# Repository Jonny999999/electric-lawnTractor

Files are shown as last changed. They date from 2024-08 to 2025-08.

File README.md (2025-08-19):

# Throttle Tune – Throttle Adapter for BLDC Motor Controllers

A microcontroller-based board with a PWM-based analog output (RC filter + buffer) to emulate a DAC.
The goal is to improve throttle response and add configurable driving modes to cheap BLDC motor controllers (e.g. 3000 W BLDC "go-kart kit" controllers).  

Currently it is used in the [electric Kettcar conversion](https://pfusch.zone/electric-kettcar.html) with a 3000 W BLDC drive, this board fixes the controller’s unusable throttle mapping and makes the vehicle smooth and controllable adding a lot of flexibility.

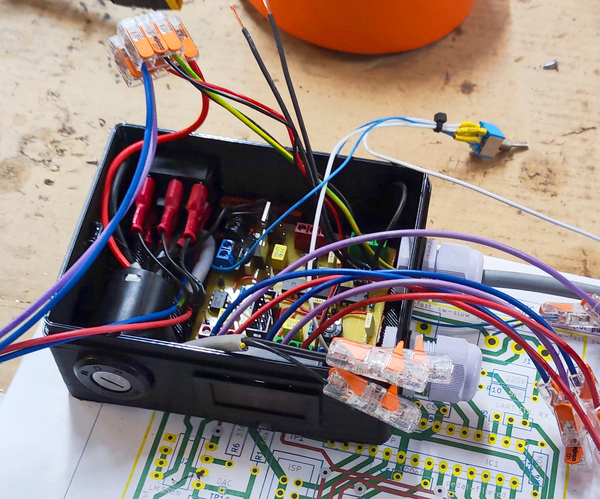
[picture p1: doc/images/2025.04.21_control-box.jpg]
  

*Control box with the custom pcb connected between throttle and motor controller*  
*Contains: PCB, key switch, battery indicator, several UI switches*

---

## Problem

Cheap BLDC controllers (such as KT-style 3000 W kits) have several issues:
- No configuration options at all
- Speed levels provided by the controller are usually defined poorly
- Only ~2 cm (~60 %) of gas pedal travel is actually used
- Jerky, hard-to-control acceleration (tiny pedal movements cause extreme changes in power - positive feedback when accelerating thus pressing the pedal more makes this even worse)

Using only the original setup makes smooth low-speed driving or child-friendly operation nearly impossible

---

## Solution

The **Throttle Tune** board sits between the analog throttle pedal (or handle) and the motor controller.  
It rescales, filters, and manipulates the signal (fading, modes...) while adding safety and convenience features.

---

## Features

### Firmware
- **Throttle remap**: use full pedal range (configure in/out ranges)
- **Ramp-up / fade**: prevents stuttering, smoother control (configurable max rate of change)
- **Speed modes**: 3 levels + hidden "Sport" mode (highly configurable - several parameters on per-mode-basis)
- **Reverse scaling**: reduced throttle in reverse
- **Buzzer alerts**: startup-, reverse-, mode switch beeps

### Hardware
- ATmega8 microcontroller
- Custom DAC output (0–5 V) to motor controller (implementation: PWM output -> lowpass -> buffer)
- CNC-milled single-sided PCB
- Through-hole components (easy to build/repair)
- 3D-printed enclosure
- Inputs: Hall pedal, reverse switch, speed selector
- Outputs: DAC to controller, buzzer

---

## Hardware

### Schematic
[pcb_throttle-tune/export/schematic.pdf](pcb_throttle-tune/export/schematic.pdf)  


### Layout


### PCB Photo
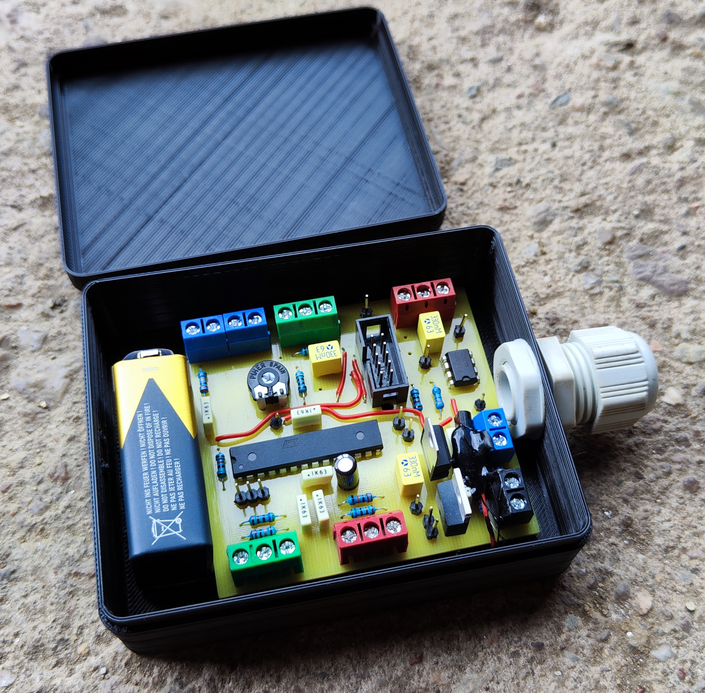
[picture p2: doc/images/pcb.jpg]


---

## Example Applications

### Electric Kettcar
Documentation: [pfusch.zone/electric-kettcar](https://pfusch.zone/electric-kettcar)

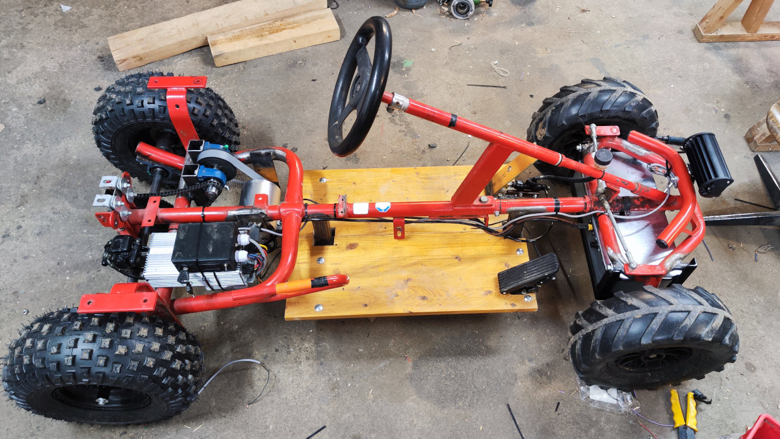
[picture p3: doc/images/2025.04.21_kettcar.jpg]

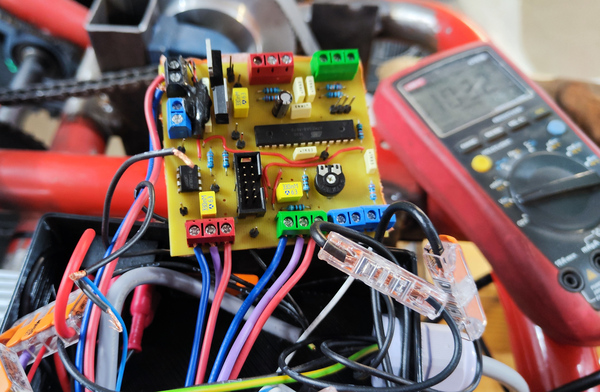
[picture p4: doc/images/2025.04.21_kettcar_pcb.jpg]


*Wiring of PCB between pedal and controller (right) and the finished vehicle (left).*

---

### Electric Lawn Tractor (temporary use-case)
Documentation: [pfusch.zone/electric-lawn-tractor](https://pfusch.zone/electric-lawn-tractor)

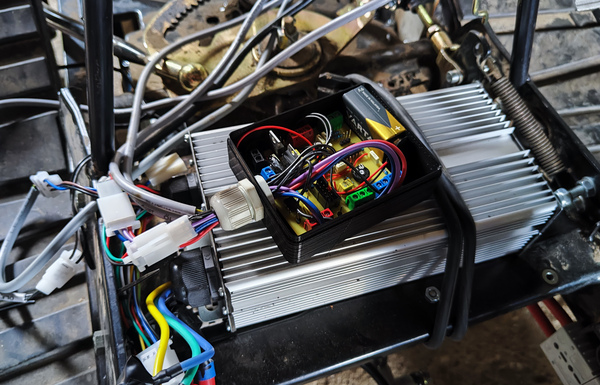
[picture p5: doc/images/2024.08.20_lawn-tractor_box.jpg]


*Throttle Tune board inside in box on top of the motor controller, battery powered (earlier project - initial but temporary use).*

---

## Repository Content
- `pcb_throttle-tune/` – KiCad project, schematic, layout exports
- `fw_throttle-tune/` – AVR firmware (ATmega8)
- `doc/images` – photos of the build and control box

---

## Usage

### Wiring
See [pcb_throttle-tune/export/layout.pdf](pcb_throttle-tune/export/layout.pdf) for what needs to be connected to which terminals.

### Adjust thresholds
Several config options (macro variables) are defined at the top of `main.c` (see detailed comments).
These include controller start/max voltage, pedal min/max voltage, idle voltage, etc.  
To calibrate:  
- Wire everything up  
- Enable `DEBUG_UART_DEBUG_OUTPUT_ENABLED`  
- Build and flash the firmware
- Connect a USB-UART adapter (header pins next to mcu, TX + GND are enough)  
- Play with the throttle and observe the UART logs to determine the values  
- Adjust the macros in `main.c` accordingly, compile, flash, try again

### Configure / Adjust modes
Driving modes are selected via 2 GPIO pins, each with its own config in the `modeConfigs[]` array.  
Parameters can be tuned per mode using this struct:
```c
//=============================
//==== Mode configuration =====
//=============================
typedef struct {
    const char *name;
    uint8_t maxPercent;     // percent of max possible speed applied at full throttle
    uint8_t maxPercentReverse;
    uint8_t beepCount;      // count beeped when entering this mode
    uint16_t rampUpStep;    // max duty increment per interval (max 1023)
    uint16_t rampUpIntervalMs; // note: must be larger than cycle time (consider when UART used alot)
    uint8_t pedalAverageWindowSize; // window size of the moving average to smooth pedal input (0 = disabled)
    // Future: pedal averaging, throttle curve, etc.
} kettcarConfig_t;
```
See comments in main.c and adjust as needed.

### Build & Flash
#### Install Requirements
```bash
yay -S avr-gcc avr-libc make
```

#### Build
```bash
cd fw_throttle-tune/
make
```

#### Flash
Connect avr controller using USBASP V2.0 ISP programmer using the 10pin connector on the pcb
```bash
cd fw_throttle-tune/
make                # compile firmware first
sudo make upload    # flash to MCU via USBasp
```
Note: Be sure to recompile before flashing, or you may upload an old build...

---

## TODO (future hardware rev)
- Add TVS diode  
- Add buzzer footprint (currently wired to spare pin and implemented in firmware, but not documented in pcb design)  
- Drop unused terminals (see notes design)
- Add reverse polarity protection
- Add onboard buck converter to be used with e.g. 72V directly not requiring external converter

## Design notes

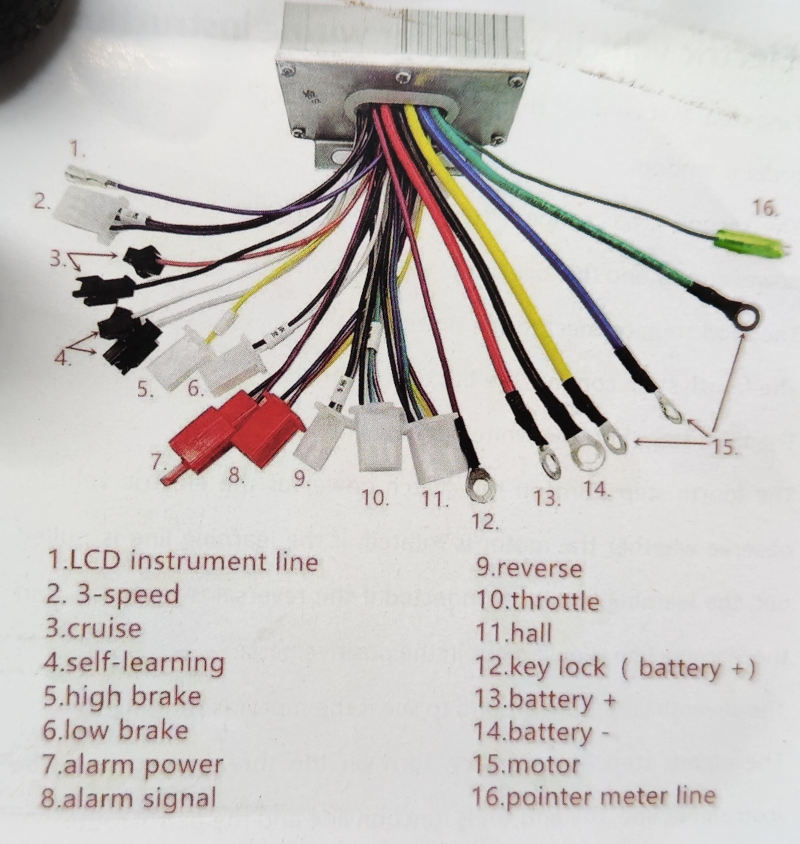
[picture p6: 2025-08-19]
doc/images/3000W-controller_wire-assignment.jpg

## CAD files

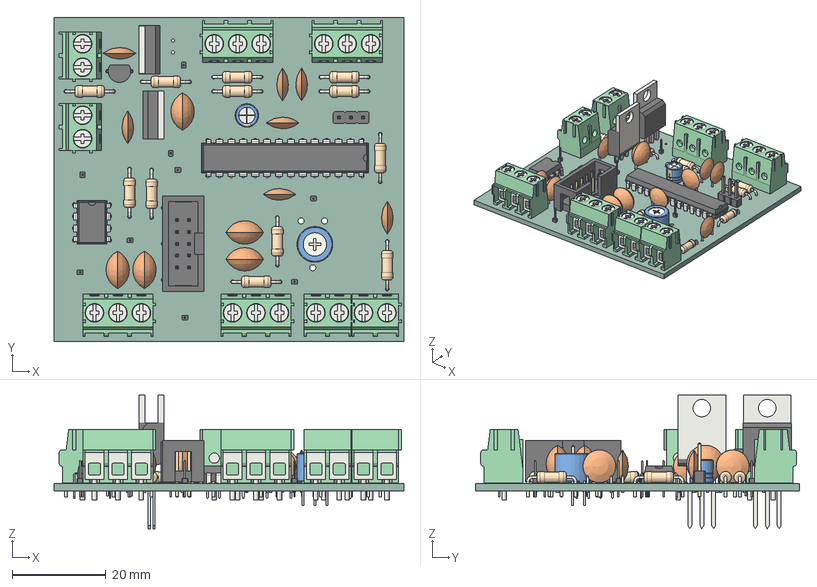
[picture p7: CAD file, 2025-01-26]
pcb_throttle-tune/export/throttle-tune.step
74.7 x 69.1 x 28.5 mm
TerminalBlock_Phoenix_PT_15_2_50_H_1x02_P500mm_Horizontal x 4
C_Disc_D70mm_W25mm_P500mm x 7
R_Axial_DIN0207_L63mm_D25mm_P1016mm_Horizontal x 12
TerminalBlock_Phoenix_PT_15_3_50_H_1x03_P500mm_Horizontal x 4
PinHeader_1x01_P100mm_Vertical x 9
Potentiometer_Bourns_3339P_Vertical
TO-92_Inline_Wide
C_Disc_D80mm_W50mm_P500mm x 5
DIP-8_W7.62mm
TO-220-3_Vertical x 2
PinHeader_1x03_P254mm_Vertical
DIP-28_W7.62mm
IDC_Header_2x05_P254mm_Vertical
CP_Radial_D50mm_P250mm
throttle-tune_PCB

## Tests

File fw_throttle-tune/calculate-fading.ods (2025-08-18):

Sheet: interval-variable_step-fixed
kettcar throttle-tune pcb: determine fading related config options for the different modes
 | rampUpIntervalMs | Resulting 0 to 100 time ms note: depending on level only e.g. 0 to 40% is actually used | Resulting time from 0 to maxDuty
 | 1 | 248 | 37 |  | CONFIG
 | 2 | 495 | 74 |  | CONTROLLER_MAX | 670
 | 3 | 743 | 111 |  | CONTROLLER_MIN | 175
 | 4 | 990 | 149
 | 5 | 1238 | 186
 | 6 | 1485 | 223 |  | rampUpStep | 2
 | 7 | 1733 | 260
 | 8 | 1980 | 297 |  | maxDuty (mode) | 15
 | 9 | 2228 | 334
 | 10 | 2475 | 371
 | 11 | 2723 | 408
 | 12 | 2970 | 446 | Goal: select config options rampUpStep and rampUpIntervalMs Howto: try different rampUpdateIntervalMs and search&select rampUpStep line to achive desired time to maxDuty / 100% Its probably a good idea to have small step for max smoothness/resolution
 | 13 | 3218 | 483
 | 14 | 3465 | 520
 | 15 | 3713 | 557
 | 16 | 3960 | 594
 | 17 | 4208 | 631
 | 18 | 4455 | 668
 | 19 | 4703 | 705
 | 20 | 4950 | 743
 | 21 | 5198 | 780
 | 22 | 5445 | 817
 | 23 | 5693 | 854
 | 24 | 5940 | 891
 | 25 | 6188 | 928
 | 26 | 6435 | 965
 | 27 | 6683 | 1002
 | 28 | 6930 | 1040
 | 29 | 7178 | 1077
 | 30 | 7425 | 1114
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

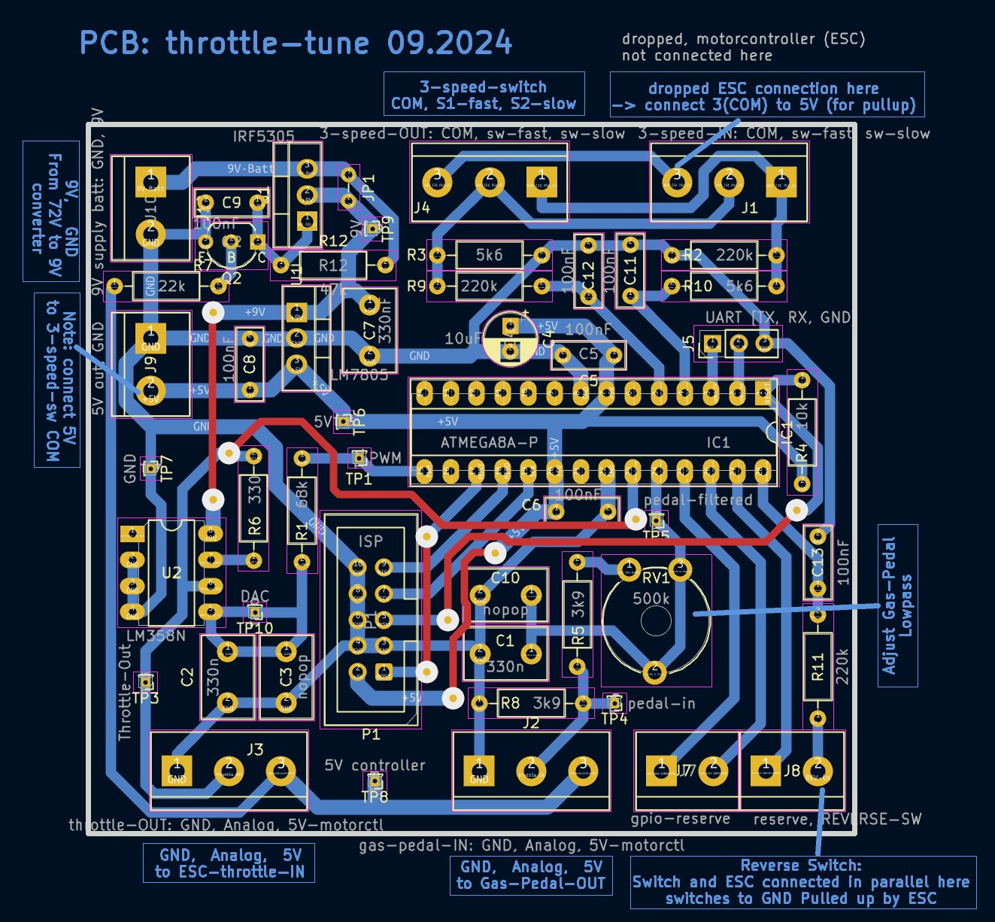
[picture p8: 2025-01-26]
pcb_throttle-tune/export/layout.jpg

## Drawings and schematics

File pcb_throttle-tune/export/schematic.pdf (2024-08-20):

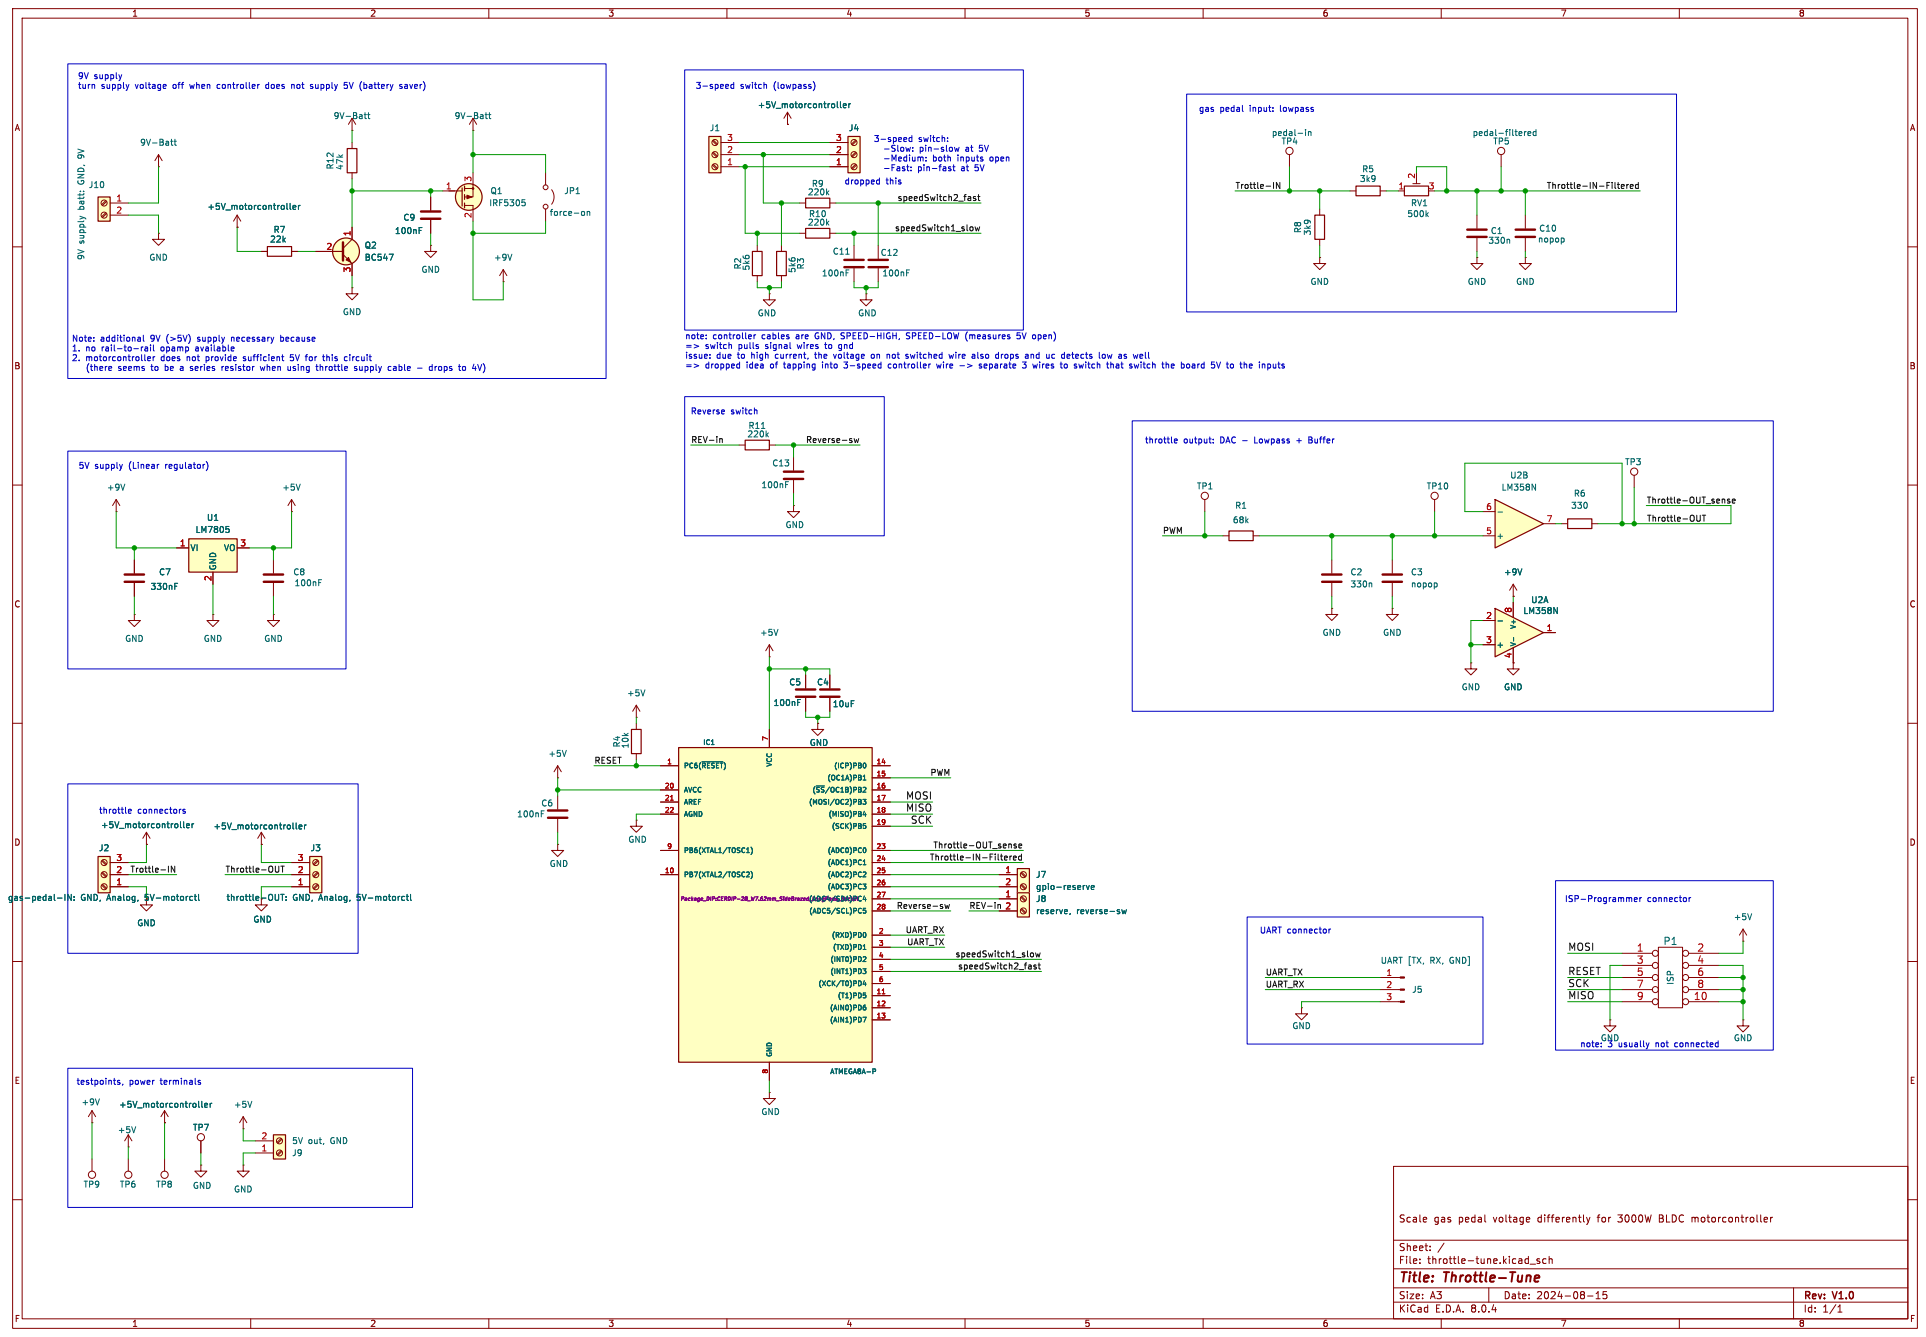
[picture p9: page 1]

IRF5305
REV-in Throttle-IN-Filtered Reverse-sw

note: 3 usually not connected

Id: 1/1 Title: Throttle-Tune

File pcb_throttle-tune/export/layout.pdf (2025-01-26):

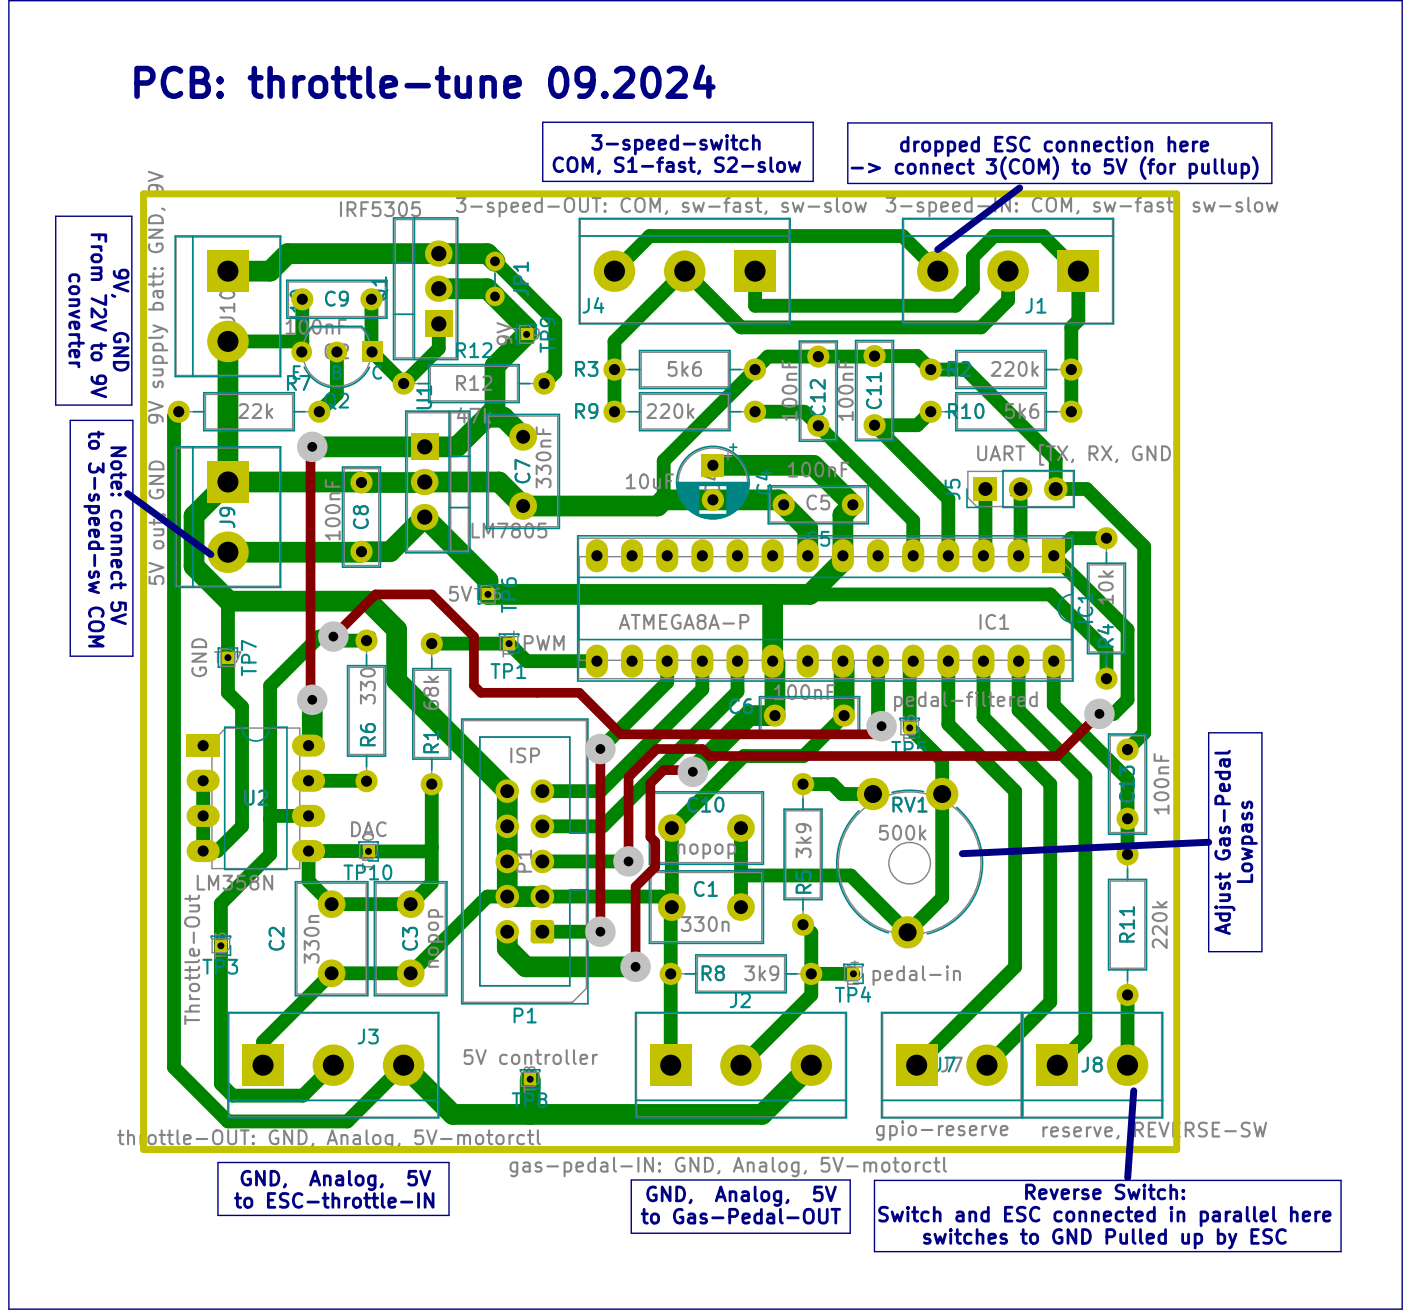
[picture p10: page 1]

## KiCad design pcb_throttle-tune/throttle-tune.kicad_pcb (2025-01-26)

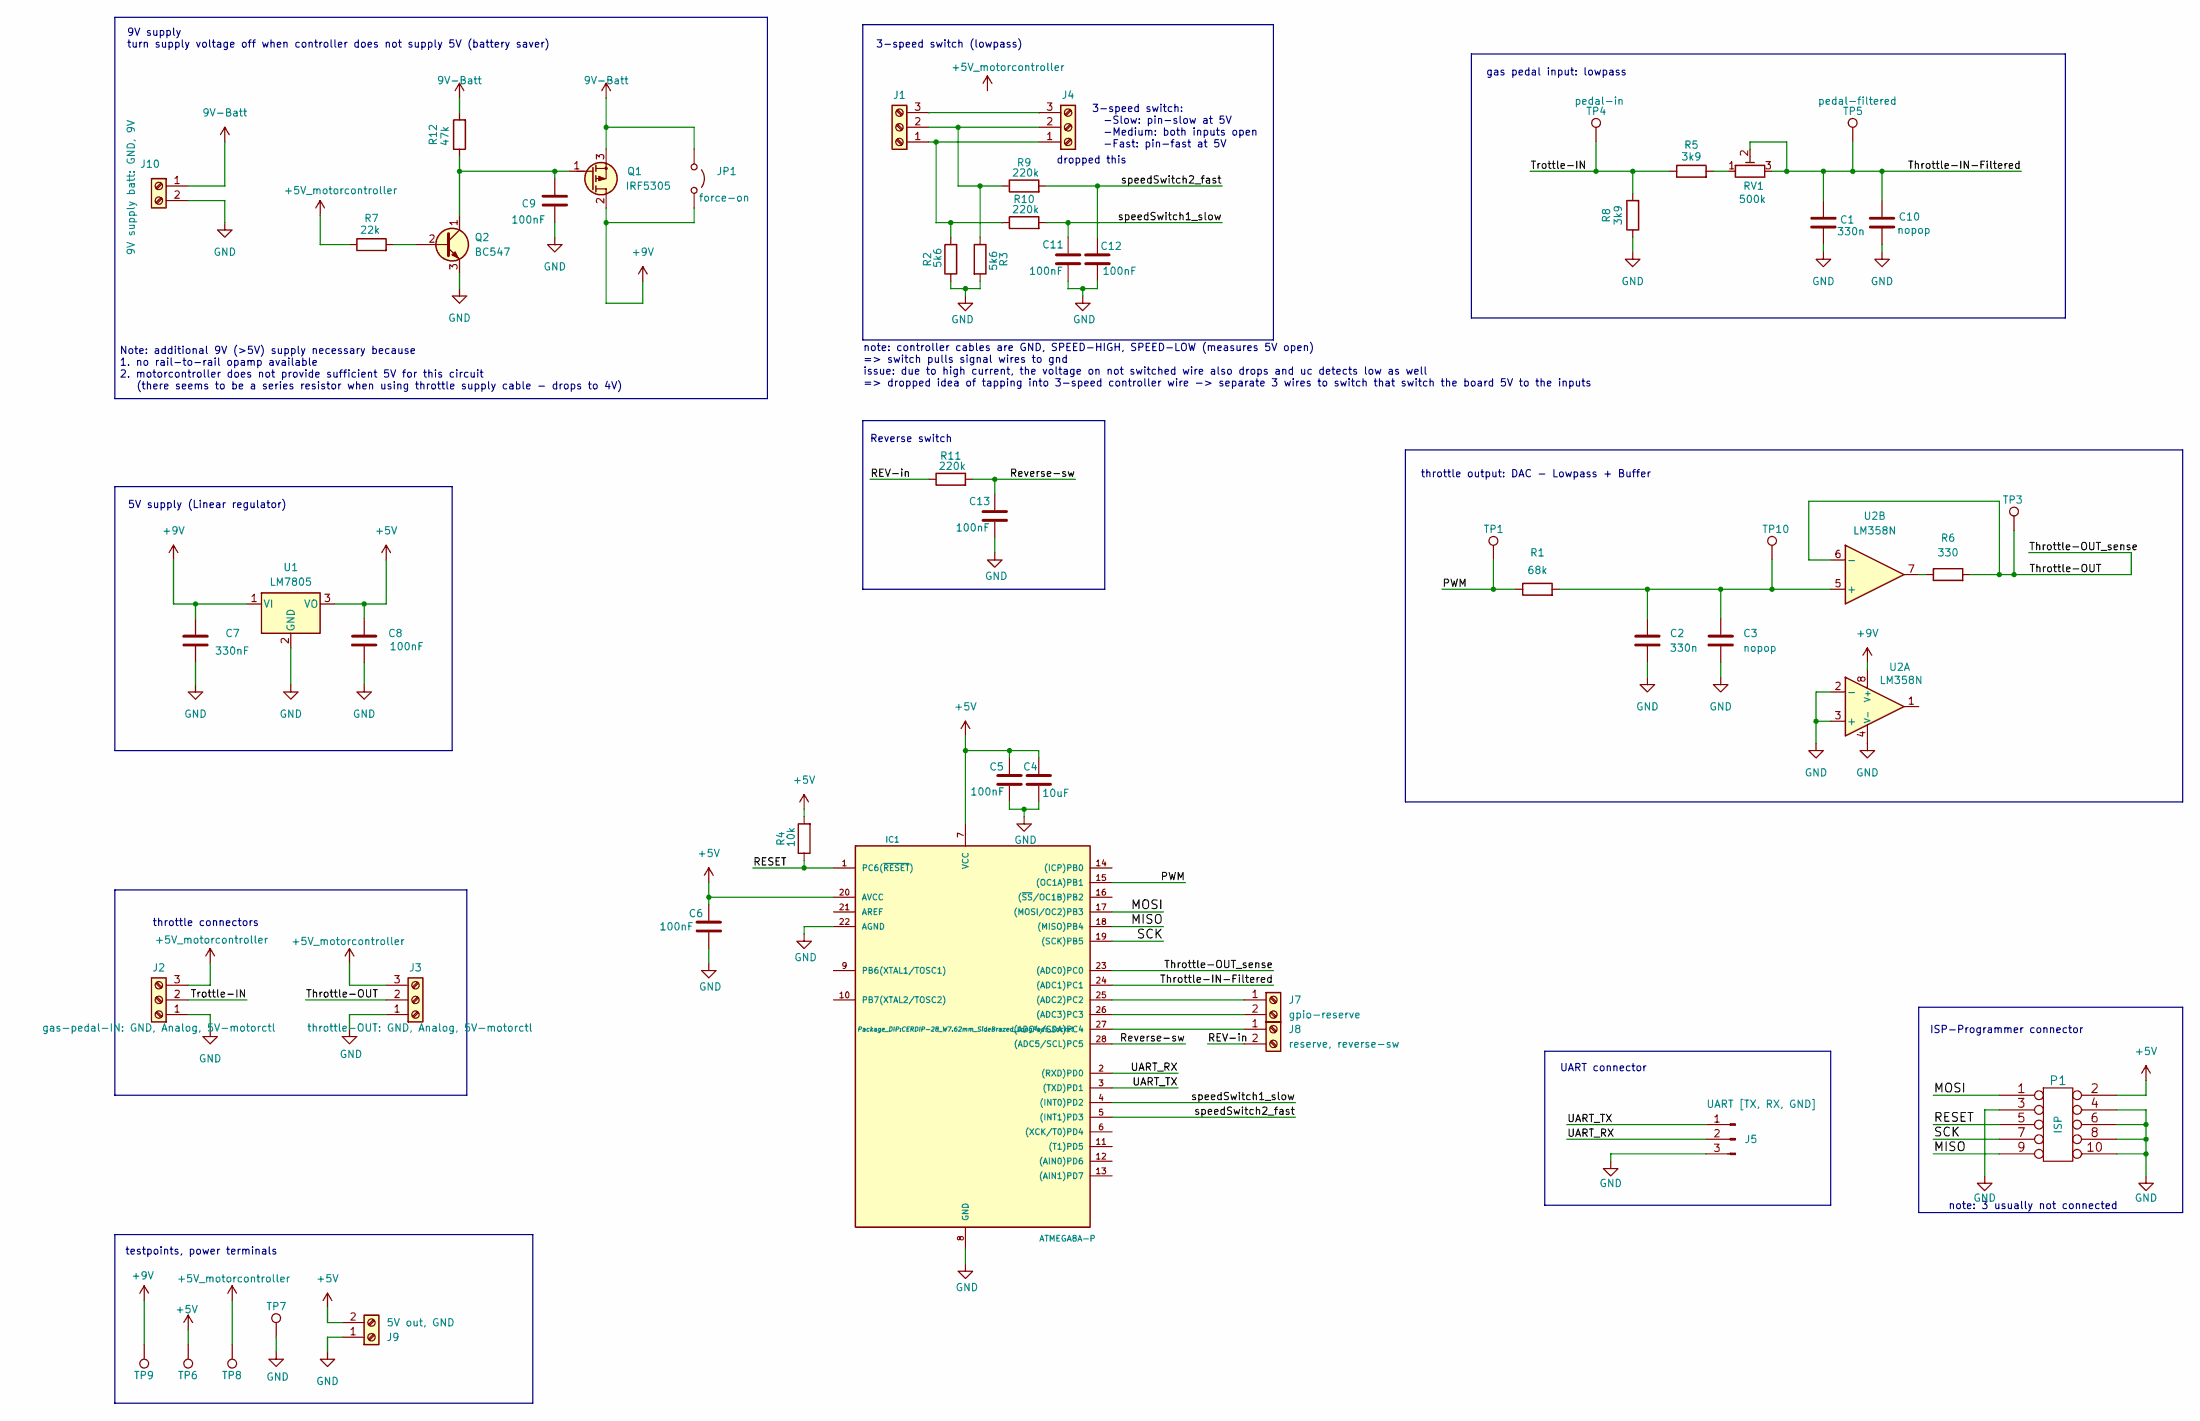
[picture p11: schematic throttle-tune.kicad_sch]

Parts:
C1, C2: 330n; C_Disc_D8.0mm_W5.0mm_P5.00mm
C3, C10: nopop; C_Disc_D8.0mm_W5.0mm_P5.00mm
C4: 10uF; CP_Radial_D5.0mm_P2.50mm
C5, C6, C8, C9, C11, C12, C13: 100nF; C_Disc_D7.0mm_W2.5mm_P5.00mm
C7: 330nF; C_Disc_D8.0mm_W5.0mm_P5.00mm
IC1: ATMEGA8A-P; CERDIP-28_W7.62mm_SideBrazed_LongPads_Socket
J1: 3-speed-IN: COM, sw-fast, sw-slow; TerminalBlock_bornier-3_P5.08mm
J2: gas-pedal-IN: GND, Analog, 5V-motorctl; TerminalBlock_bornier-3_P5.08mm
J3: throttle-OUT: GND, Analog, 5V-motorctl; TerminalBlock_bornier-3_P5.08mm
J4: 3-speed-OUT: COM, sw-fast, sw-slow; TerminalBlock_bornier-3_P5.08mm
J5: UART [TX, RX, GND]; PinHeader_1x03_P2.54mm_Vertical
J7: gpio-reserve; TerminalBlock_bornier-2_P5.08mm
J8: reserve, reverse-sw; TerminalBlock_bornier-2_P5.08mm
J9: 5V out, GND; TerminalBlock_bornier-2_P5.08mm
J10: 9V supply batt: GND, 9V; TerminalBlock_bornier-2_P5.08mm
JP1: force-on; Jumper_P2.54mm_D0.7mm
P1: ISP; IDC-Header_2x05_P2.54mm_Vertical
Q1: IRF5305; TO-220-3_Vertical
Q2: BC547; TO-92_Inline_Wide_CBE
R1: 68k; R_Axial_DIN0207_L6.3mm_D2.5mm_P10.16mm_Horizontal
R2, R3: 5k6; R_Axial_DIN0207_L6.3mm_D2.5mm_P10.16mm_Horizontal
R4: 10k; R_Axial_DIN0207_L6.3mm_D2.5mm_P10.16mm_Horizontal
R5, R8: 3k9; R_Axial_DIN0207_L6.3mm_D2.5mm_P10.16mm_Horizontal
R6: 330; R_Axial_DIN0207_L6.3mm_D2.5mm_P10.16mm_Horizontal
R7: 22k; R_Axial_DIN0207_L6.3mm_D2.5mm_P10.16mm_Horizontal
R9, R10, R11: 220k; R_Axial_DIN0207_L6.3mm_D2.5mm_P10.16mm_Horizontal
R12: 47k; R_Axial_DIN0207_L6.3mm_D2.5mm_P10.16mm_Horizontal
RV1: 500k; Potentiometer_Piher_PT-10-V10_Vertical
TP1: PWM; PinHeader_1x01_P1.00mm_Vertical
TP3: Throttle-Out; PinHeader_1x01_P1.00mm_Vertical
TP4: pedal-in; PinHeader_1x01_P1.00mm_Vertical
TP5: pedal-filtered; PinHeader_1x01_P1.00mm_Vertical
TP6: 5V; PinHeader_1x01_P1.00mm_Vertical
TP7: GND; PinHeader_1x01_P1.00mm_Vertical
TP8: 5V controller; PinHeader_1x01_P1.00mm_Vertical
TP9: 9V; PinHeader_1x01_P1.00mm_Vertical
TP10: DAC; PinHeader_1x01_P1.00mm_Vertical
U1: LM7805; TO-220-3_Vertical
U2: LM358N; DIP-8_W7.62mm_LongPads

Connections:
9V-Batt: J10.1, JP1.1 (A), Q1.3 (S), R12.2
+5V: C4.1, C5.1, C6.1, C8.1, IC1.7 (VCC), IC1.20 (AVCC), J9.2, P1.2, R4.2, TP6.1, U1.3 (VO)
+5V_motorcontroller: J2.3, J3.3, R7.1, TP8.1
+9V: C7.1, JP1.2 (B), Q1.2 (D), TP9.1, U1.1 (VI), U2.8 (V+)
/MISO: IC1.18 ((MISO)PB4), P1.9
/MOSI: IC1.17 ((MOSI/OC2)PB3), P1.1
/PWM: IC1.15 ((OC1A)PB1), R1.1, TP1.1
/RESET: IC1.1 (PC6(~RESET)), P1.5, R4.1
/REV-in: J8.2, R11.1
/Reverse-sw: C13.1, IC1.28 ((ADC5/SCL)PC5), R11.2
/SCK: IC1.19 ((SCK)PB5), P1.7
/Throttle-IN-Filtered: C1.1, C10.1, IC1.24 ((ADC1)PC1), RV1.2, RV1.3, TP5.1
/Throttle-OUT: IC1.23 ((ADC0)PC0), J3.2, R6.2, TP3.1, U2.6 (-)
/Trottle-IN: J2.2, R5.1, R8.2, TP4.1
/UART_RX: IC1.2 ((RXD)PD0), J5.2
/UART_TX: IC1.3 ((TXD)PD1), J5.1
/speedSwitch1_slow: C11.1, IC1.4 ((INT0)PD2), R10.2
/speedSwitch2_fast: C12.1, IC1.5 ((INT1)PD3), R9.2
GND: C1.2, C2.2, C3.2, C4.2, C5.2, C6.2, C7.2, C8.2, C9.2, C10.2, C11.2, C12.2, C13.2, IC1.8 (GND), IC1.22 (AGND), J2.1, J3.1, J5.3, J9.1, J10.2, P1.3, P1.4, P1.6, P1.8, P1.10, Q2.3 (E), R2.1, R3.2, R8.1, TP7.1, U1.2 (GND), U2.2 (-), U2.3 (+), U2.4 (V-)
unnamed: IC1.25 ((ADC2)PC2), J7.1
unnamed: IC1.26 ((ADC3)PC3), J7.2
unnamed: IC1.27 ((ADC4/SDA)PC4), J8.1
unnamed: J1.1, J4.1, R2.2, R10.1
unnamed: J1.2, J4.2, R3.1, R9.1
unnamed: J1.3, J4.3
unnamed: C9.1, Q1.1 (G), Q2.1 (C), R12.1
unnamed: Q2.2 (B), R7.2
unnamed: R5.2, RV1.1
unnamed: R6.1, U2.7
unnamed: C2.1, C3.1, R1.2, TP10.1, U2.5 (+)

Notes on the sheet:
throttle output: DAC - Lowpass + Buffer
note: controller cables are GND, SPEED-HIGH, SPEED-LOW (measures 5V open) => switch pulls signal wires to gnd issue: due to high current, the voltage on not switched wire also drops and uc detects low as well => dropped idea of tapping into 3-speed controller wire -> separate 3 wires to switch that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
throttle connectors
UART connector
3-speed switch (lowpass)
9V supply turn supply voltage off when controller does not supply 5V (battery saver)
note: 3 usually not connected
Note: additional 9V (>5V) supply necessary because 1. no rail-to-rail opamp available 2. motorcontroller does not provide sufficient 5V for this circuit (there seems to be a series resistor when using throttle supply cable - drops to 4V)
dropped this
gas pedal input: lowpass
5V supply (Linear regulator)
testpoints, power terminals
ISP-Programmer connector
3-speed switch: -Slow: pin-slow at 5V -Medium: both inputs open -Fast: pin-fast at 5V
Reverse switch

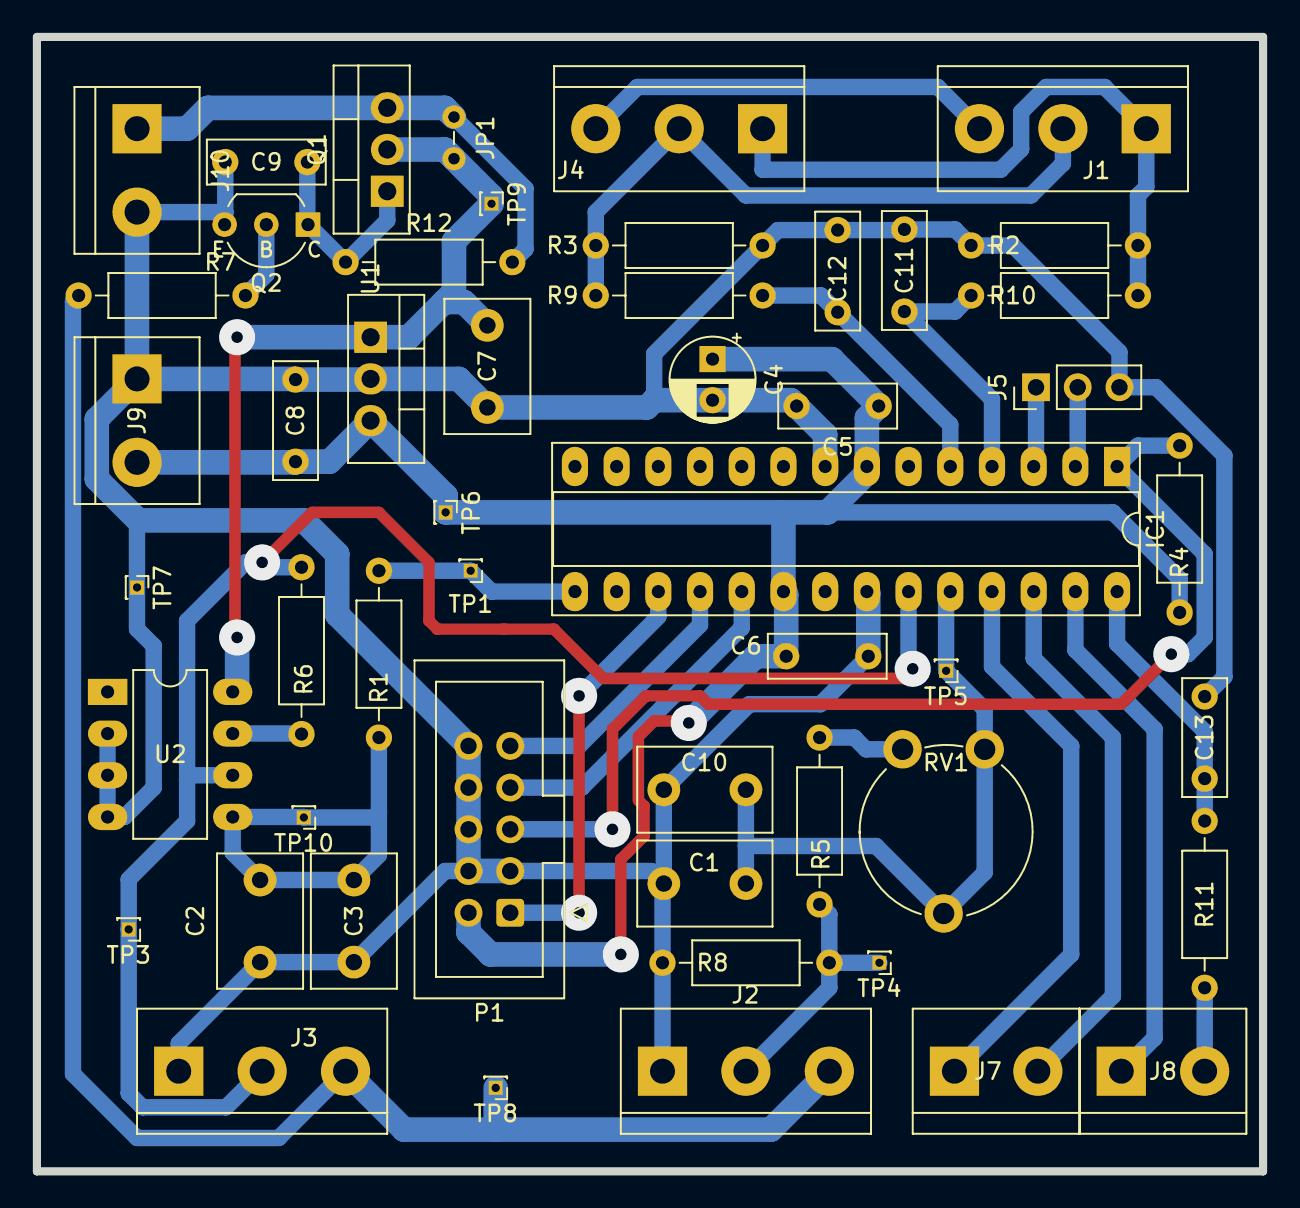
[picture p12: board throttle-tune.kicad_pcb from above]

Board: 2 copper layers, 74.7 x 69.1 mm, 51 parts (0 on the bottom side), 30 nets.

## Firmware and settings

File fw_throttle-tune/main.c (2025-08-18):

#include <avr/io.h>
#include <util/delay.h>
#include "usart.h"
#include "a2d.h"

#include "gpio.h"
#include "time.h"
#include "pwm.h"
#include "stdbool.h"

//====================
//====== config ======
//====================
// debugging
#define DEBUG_UART_DEBUG_OUTPUT_ENABLED 0 // log several variables for debugging the firmware
#define DEBUG_UART_DEBUG_OUTPUT_INTERVAL_MS 500 // interval the variables are logged (limit rate to have cycles for rest of firmware)
#define DEBUG_LOG_CYCLE_SPEED 0 // log main loop cycle count per 1000ms (to determine if set intervals are even realistic -> should always be higher than 1000 so we have 1ms resolution)
#define DEBUG_PASS_THROUGH 0 //if defined duty/output voltage is set to the same as input voltage (test hardware)

// thresholds (adc values, determined/tested with debug output)
#define GAS_PEDAL_MAX 630 // actual 660 no force / 697 with force
#define GAS_PEDAL_MIN 200 // actual 171 - note weird behaviour: when pressing decreases to 160 first then increases to MAX 

// thresholds the out voltage is scaled in between (0-100% speed)
#define CONTROLLER_START 250  // 250 starts, 246 stops (TODO: start higher?)
#define CONTROLLER_MAX 600 // hard to determine precisely

#define CONTROLLER_IDLE_DUTY 190 // keep some voltage when off, to prevent controller from going into fault mode
#define CONTROLLER_FULL_SPEED_DUTY 800
// duty set at 100% target speed (slightly higher than CONTROLLER_MAX ) to be sure to reach actual maximum speed even when CONTROLLER_MAX is slightly too low / we got noise

//--- fading ---
// track/estimate motor rpm/rolling out for quicker resume (start fading up from memory instead of 0)
// 6, 50ms -> 4s to decay from 100% to 0% 
#define DUTY_MEMORY_DECAY_INTERVAL_MS 50
#define DUTY_MEMORY_DECAY_STEP 4 // max 1023

// misc
#define BEEP_AT_REV_SW_CHANGE 1
#define PEDAL_SAMPLE_INTERVAL_MS 5 // minimum ms passed between sampling the pedal adc -> significantly affects moving average, but compensated by macro during config
#define PEDAL_SMOOTHING_MAX_WINDOW_SIZE 255 // max history of pedal adc values that can be kept for moving average



//--- configure GPIO Pins ---
// buzzer
const GPIO_Pin buzzerPin = {PC3, &PORTC, &DDRC, &PINC};

// speed switch
const GPIO_Pin speedSwitch_slow = {PD2, &PORTD, &DDRD, &PIND};
const GPIO_Pin speedSwitch_fast = {PD3, &PORTD, &DDRD, &PIND};
const GPIO_Pin reverseSwitch = {PC5, &PORTC, &DDRC, &PINC};



//=============================
//==== Mode configuration =====
//=============================
typedef struct {
    const char *name;
    uint8_t maxPercent;     // percent of max possible speed applied at full throttle
    uint8_t maxPercentReverse;
    uint8_t beepCount;      // count beeped when entering this mode
    uint16_t rampUpStep;    // max duty increment per interval (max 1023)
    uint16_t rampUpIntervalMs; // note: must be larger than cycle time (consider when UART used alot)
    uint8_t pedalAverageWindowSize; // window size of the moving average to smooth pedal input (0 = disabled)
    // Future: pedal averaging, throttle curve, etc.
} kettcarConfig_t;

// global variable to track the active mode
uint8_t currentModeIndex = 0;

#define NUM_MODES 4
// have readable names for config index
#define MODE_SLOW   0
#define MODE_MEDIUM 1
#define MODE_FAST   2
#define MODE_SPORT  3
// note that speed switch also affects / limits the controller (sw connected to controller as well to limit top speed)
// so maxPercent is not directly comparable between modes (e.g. even all at 100%: already slower in slow mode)
// configure parameters of the selectable modes:

// helper macros to determine parameters
#define TIME_FROM_0_TO_100(rampUpStep, rampUpIntervalMs) ((CONTROLLER_MAX - CONTROLLER_START) * rampUpIntervalMs / rampUpStep)
#define AVERAGE_TIME_MS_TO_WINDOW_SIZE(timeMs) ((timeMs) / PEDAL_SAMPLE_INTERVAL_MS)
#define MAX_AVERAGE_WINDOW_MS (PEDAL_SMOOTHING_MAX_WINDOW_SIZE * PEDAL_SAMPLE_INTERVAL_MS)

const kettcarConfig_t modeConfigs[NUM_MODES] = {
    {
        .name = "Slow",
        .maxPercent = 15,
        .maxPercentReverse = 8,
        .beepCount = 1,
        // 1, 30ms -> 2.2s from 0 to 15% 
        .rampUpStep = 1,
        .rampUpIntervalMs = 30,
        .pedalAverageWindowSize = AVERAGE_TIME_MS_TO_WINDOW_SIZE(250) //note: time may not exceed MAX_AVERAGE_WINDOW_MS
    },
    {
        .name = "Medium",
        .maxPercent = 40,
        .maxPercentReverse = 30,
        .beepCount = 2,
        // 1, 15ms -> 2.9s from 0 to 40%
        .rampUpStep = 1,
        .rampUpIntervalMs = 15,
        .pedalAverageWindowSize = AVERAGE_TIME_MS_TO_WINDOW_SIZE(250)
    },
    {
        .name = "Fast",
        .maxPercent = 92,
        .maxPercentReverse = 50,
        // 3, 20ms -> 3s from 0 to 92%
        .beepCount = 3,
        .rampUpStep = 3,
        .rampUpIntervalMs = 20,
        .pedalAverageWindowSize = AVERAGE_TIME_MS_TO_WINDOW_SIZE(250)
    },
    {
        .name = "Sport",
        .maxPercent = 100,
        .maxPercentReverse = 100,
        .beepCount = 6,
        // ramp disabled - increase by large amount every cycle
        .rampUpStep = 1024,
        .rampUpIntervalMs = 0,
        .pedalAverageWindowSize = AVERAGE_TIME_MS_TO_WINDOW_SIZE(200)
    }
};



// custom delay function to prevent error:
// "__builtin_avr_delay_cycles expects a compile time integer constant"
void delay_ms(uint32_t ms) {
    while (ms--) {
        // Each iteration takes approximately 1 ms
        _delay_ms(1);
    }
}

// helper function to beep for certain count
void beepCustom(uint8_t count, uint32_t msOn, uint32_t msOff){
  for (int i = 1; i <= count; i++)
  {
    GPIO_Set(&buzzerPin);
    delay_ms(msOn);
    GPIO_Clear(&buzzerPin);
    if (i < count) // prevent unnecessary delay after last beep
      delay_ms(msOff);
  }
}

void beep(uint8_t count){
  beepCustom(count, 80, 70);
}

void beepLong(uint8_t count){
  beepCustom(count, 300, 100);
}



// function that evaluates if switch to sport mode sequence is entered and switches to sport mode
#define MODE_SPORT_ACTIVATION_TIME_WINDOW_MS 3000
#define MODE_SPORT_ACTIVATION_REVERSE_SW_EDGE_COUNT 3
void checkForSportModeActivation(void) {
    static uint8_t revToggleCount = 0;
    static bool lastRevState = false;
    static uint32_t timestamp_firstToggle = 0;

    if (!GPIO_Read(&speedSwitch_fast)) {
        // Not in fast mode, reset sport toggle tracking
        revToggleCount = 0;
        timestamp_firstToggle = 0;
        lastRevState = GPIO_Read(&reverseSwitch);
        return;
    }

    bool currentRevState = GPIO_Read(&reverseSwitch);

    if (!lastRevState && currentRevState) {
        // Rising edge detected
        uint32_t now = time_get_ms();

        if (timestamp_firstToggle == 0 || now - timestamp_firstToggle > MODE_SPORT_ACTIVATION_TIME_WINDOW_MS) {
            // Restart tracking
            revToggleCount = 1;
            timestamp_firstToggle = now;
        } else {
            revToggleCount++;
            if (revToggleCount >= MODE_SPORT_ACTIVATION_REVERSE_SW_EDGE_COUNT) {
              _delay_ms(100);
              if (currentModeIndex == MODE_SPORT) {
                currentModeIndex = MODE_FAST;
                beep(modeConfigs[MODE_FAST].beepCount);
                printf("\nAlready in sportmode -> Switched to mode %s\n", modeConfigs[currentModeIndex].name);
              } else {
                currentModeIndex = MODE_SPORT;
                beep(modeConfigs[MODE_SPORT].beepCount);
                printf("\nSwitched to mode %s\n", modeConfigs[currentModeIndex].name);
              }
                revToggleCount = 0;
                timestamp_firstToggle = 0;
            }
        }
    }

    lastRevState = currentRevState;
}



// function that updates the currently selected config depending on speed switch position
#define MODE_CONFIRM_DELAY_MS 500 // only beep after mode is active for that time
void handleSlowMediumFastModeSwitch(void) {
    static uint8_t lastStableIndex = 255;
    static uint32_t timestamp_lastChange = 0;

    if (GPIO_Read(&speedSwitch_fast) && currentModeIndex == MODE_SPORT) {
        // Dont override sport mode
        return;
    }

    bool slow = GPIO_Read(&speedSwitch_slow);
    bool fast = GPIO_Read(&speedSwitch_fast);
    uint8_t newIndex;
    if (slow && fast) {
        // Invalid combo, skip update
        return;
    } else if (slow) {
        newIndex = MODE_SLOW; // Slow
    } else if (fast) {
        newIndex = MODE_FAST; // Fast
    } else {
        newIndex = MODE_MEDIUM; // Medium
    }

    if (newIndex != currentModeIndex) {
        currentModeIndex = newIndex;
        timestamp_lastChange = time_get_ms();
        return;
    }

    // Stable long enough for confirmation beep?
    if (currentModeIndex != lastStableIndex && time_get_ms() - timestamp_lastChange > MODE_CONFIRM_DELAY_MS) {
      if (time_get_ms() > MODE_CONFIRM_DELAY_MS + 500) // prevent beeping directly after startup
        beep(modeConfigs[currentModeIndex].beepCount);
      printf("\nSwitched to mode %s\n", modeConfigs[currentModeIndex].name);
      lastStableIndex = currentModeIndex;
    }
}




// Function to calculate the moving average of the last N pedal values
uint16_t GetSmoothedPedalInput(uint16_t newPedalValue, uint8_t windowSize) {
  // Array to store past pedal values
  static uint16_t pedalHistory[PEDAL_SMOOTHING_MAX_WINDOW_SIZE] = {0};
  static uint8_t pedalHistoryIndex = 0;

  // return same value when window is 0 or 1 aka disabled
  if (windowSize < 2)
    return newPedalValue;

  // Add new value to the history array
  pedalHistory[pedalHistoryIndex] = newPedalValue;
  
  // Move to the next index, wrapping around the array
  pedalHistoryIndex = (pedalHistoryIndex + 1) % windowSize;
  
  // Calculate the sum of the last windowSize values
  uint32_t sum = 0;
  for (uint8_t i = 0; i < windowSize; i++) {
      sum += pedalHistory[i];
  }

  // Return the average 
  return sum / windowSize;
}





int main(void)
{
  // init custom time functions
  // (tracking timestamp in ms since startup in a variable using timer+ISR)
  time_init();

  // init PWM
  pwm_initFastPwmTimer1(1023, 1); //10 bit res, no prescaler

  // init UART
  uart_init();
  uart_sendStr("hello world\n");


  // --- init GPIO pins ---
  // init output
  GPIO_Init(&buzzerPin, 1); // init buzzer as output
  // init inputs
  GPIO_Init(&speedSwitch_slow, 0);
  GPIO_Init(&speedSwitch_fast, 0);
  GPIO_Init(&reverseSwitch, 0);


  // --- variables ---
  uint16_t adcInputGasPedal = 0;
  uint16_t pedalPercent_x10;
  uint16_t dutyTarget = CONTROLLER_IDLE_DUTY;
  uint16_t duty = CONTROLLER_IDLE_DUTY;
  uint16_t dutyMemory = CONTROLLER_IDLE_DUTY;
  bool lastRevSwState = false;
  uint32_t timestamp_lastPedalSample = 0;
  uint32_t timestamp_lastCycleCountLogged = 0;
  uint32_t timestamp_lastDebugOutput = 0;
  uint32_t cycleCount = 0;

  // fading
  static uint32_t timestamp_lastRampUpdate = 0;
  static uint32_t timestamp_lastDutyMemoryUpdate = 0;

  // beep at startup:
  beep(3);



  while (1)
  {
    //========================
    //===== speed-switch =====
    //========================
    checkForSportModeActivation();
    handleSlowMediumFastModeSwitch();
    const kettcarConfig_t *currentConfig = &modeConfigs[currentModeIndex];

    //TODO: handle reverse switch input


    //======================================
    //===== read + interpret gas-pedal =====
    //======================================
    if (time_msPassedSince(timestamp_lastPedalSample) > PEDAL_SAMPLE_INTERVAL_MS){
      timestamp_lastPedalSample = time_get_ms();

      // sample adc - TODO: add multisampling?
      adcInputGasPedal = ReadChannel(1); // PC5

      // calculate gas pedal percentage
      if (adcInputGasPedal <= GAS_PEDAL_MIN)
        pedalPercent_x10 = 0;
      else if (adcInputGasPedal >= GAS_PEDAL_MAX)
        pedalPercent_x10 = 1000;
      else
        pedalPercent_x10 = (uint32_t)(adcInputGasPedal - GAS_PEDAL_MIN) * 1000 / (GAS_PEDAL_MAX - GAS_PEDAL_MIN);

      // smooth out pedal input (remove peaks)
      pedalPercent_x10 = GetSmoothedPedalInput(pedalPercent_x10, currentConfig->pedalAverageWindowSize);
    }

    //======================================
    //====== read back output (debug) ======
    //======================================
#if DEBUG_UART_DEBUG_OUTPUT_ENABLED
    //(generated analog voltage via pwm)
    uint16_t adcOutput = ReadChannel(0); // PC4  - measure generated output voltage for debugging
    // calculate motor percentage from output voltage (for logging)
    uint16_t motorPercent_x10;
    if (adcOutput <= CONTROLLER_START)
      motorPercent_x10 = 0;
    else if (adcOutput >= CONTROLLER_MAX)
      motorPercent_x10 = 1000;
    else
      motorPercent_x10 = (uint32_t)(adcOutput - CONTROLLER_START) * 1000 / (CONTROLLER_MAX - CONTROLLER_START);
    // note: tis is the actual resulted percentage, when using `duty` instead of `adcOutput` you get the target motor percentage
#endif


    //==============================
    //===== define target duty =====
    //==============================
    // max duty is different when reversing
    uint8_t maxPercent;
    bool currentRevSwState = GPIO_Read(&reverseSwitch);

#if BEEP_AT_REV_SW_CHANGE
    if (lastRevSwState && !currentRevSwState) // falling edge - reverse just turned off
      beep(1);
    else if (!lastRevSwState && currentRevSwState) // rising edge - reverse just turned on
      beepLong(1);
    lastRevSwState = currentRevSwState;
#endif

#if DEBUG_PASS_THROUGH
    // 1:1 output (no scaling)
    duty = adcInputGasPedal;
#else

    if (currentRevSwState)
      maxPercent =  currentConfig->maxPercentReverse;
    else
      maxPercent = currentConfig->maxPercent;

    // calculate max allowed duty according to range
    uint16_t dutyRange = (uint32_t)(CONTROLLER_MAX - CONTROLLER_START) * maxPercent / 100;

    // calculate duty
    if (pedalPercent_x10 == 0)
      dutyTarget = CONTROLLER_IDLE_DUTY; // off but maintain some voltage
    else if (pedalPercent_x10 >= 1000)
      dutyTarget = dutyRange + CONTROLLER_START;
    else
      dutyTarget = (uint32_t)pedalPercent_x10 * dutyRange / 1000 + CONTROLLER_START;
      // duty = (uint32_t)(maxDuty-CONTROLLER_START) *1000 / (GAS_PEDAL_MAX - GAS_PEDAL_MIN)  * (adcInputGasPedal - GAS_PEDAL_MIN) / 1000 + CONTROLLER_START; //without rounding error


    //==================================
    //===== manipulate actual duty =====
    //==================================
    // Fade up
    if (dutyTarget <= duty) // ramp down instantly
      duty = dutyTarget;
    else if (dutyTarget < dutyMemory) // motor probably already turning faster than target -> set immediately
      duty = dutyMemory;
    else if (duty < dutyMemory) // estimated current motor speed less than target but still more than current - skip ramping to estimated current rpm duty again
      duty = dutyMemory;
    else if (dutyTarget - duty < currentConfig->rampUpStep) // set to exact target when differs less than increment
      duty = dutyTarget;
    else if (duty < CONTROLLER_START) //immediately start at controller start value
        duty = CONTROLLER_START;
    else { // ramp up slowly 
      if (time_msPassedSince(timestamp_lastRampUpdate) >= currentConfig->rampUpIntervalMs) {
          duty += currentConfig->rampUpStep;
          timestamp_lastRampUpdate = time_get_ms();
      }
  }

    // variable to estimate/track motor rpm (motor does not immediately stop when duty is reduced)
    // used for faster resume when pressing pedal again while rolling out
  if (duty > dutyMemory) { // update immediately if current duty is larger
    dutyMemory = duty;
    // decrease slowly when below (running out)
  } else if (time_msPassedSince(timestamp_lastDutyMemoryUpdate) >= DUTY_MEMORY_DECAY_INTERVAL_MS) {
    // TODO: decrease more/less depending on current duty?
      if (dutyMemory < DUTY_MEMORY_DECAY_STEP)
          dutyMemory = 0;
      else
          dutyMemory -= DUTY_MEMORY_DECAY_STEP;
      timestamp_lastDutyMemoryUpdate = time_get_ms();
  }

  // clip actual applied duty to configured controller values:
  // 1. duty should never be lower than idle (prevent wire defect detection)
  if (duty < CONTROLLER_IDLE_DUTY) // usually in idle (target duty = 0)
    duty = CONTROLLER_IDLE_DUTY;
  // add additional threshold when max duty is desired
  // 2. set to even higher duty when max-speed is requested to ensure the voltage is certainly exceeded
  else if (duty >= CONTROLLER_MAX) // usually in sport mode only
    duty = CONTROLLER_FULL_SPEED_DUTY;

#endif // end of else from #ifdef DEBUG_PASS_THROUGH


    //==========================
    //===== apply new duty =====
    //==========================
    pwm_setDutyCycle(duty);


    //=======================
    //======= logging =======
    //=======================
#if DEBUG_UART_DEBUG_OUTPUT_ENABLED
    // limite output to set interval
    if (time_msPassedSince(timestamp_lastDebugOutput) > DEBUG_UART_DEBUG_OUTPUT_INTERVAL_MS){
      timestamp_lastDebugOutput = time_get_ms();
      printf("adcIn=%04d, adcOut=%04d, duty=%04d -- dutyTarget=%04d, dutyMemory=%04d, pedalPercent=%2d, motorPercent=%2d.%d (level/max=%d%%)\n",
             adcInputGasPedal, adcOutput, duty, dutyTarget, dutyMemory,
             pedalPercent_x10 / 10, motorPercent_x10 / 10, motorPercent_x10 % 10, maxPercent);
    }
#endif

#if DEBUG_LOG_CYCLE_SPEED
    // Results with this option enabled 2025.05.01:
    // 1. only this output enabled:
    //   - in IDLE:          "debug: counted 11441 loop cycles the last 1000ms" (slow mode)
    //   - in FULL-THROTTLE: "debug: counted 5306  loop cycles the last 1000ms" (slow mode)
    //   - in FULL-THROTTLE: "debug: counted 5264  loop cycles the last 1000ms" (fast mode)

    // 2. full UART debug output every cycle:
    //   - IDLE/FULL-THROTTLE: "debug: counted 7 loop cycles the last 1000ms"
    //   -> pedal percent increases/decreases very slowly, motor takes ~15s to stop in slow mode
    //  TODO: If cycle count drops below 1000 accurate timing is no longer ensured -> Warn/reduce?

    // 3. full UART debug output every 500ms:
    //   - IDLE:          debug: counted 861 loop cycles the last 1000ms (medium mode)
    //   - FULL-THROTTLE: debug: counted 635 loop cycles the last 1000ms (medium mode)


    if (time_msPassedSince(timestamp_lastCycleCountLogged) > 1000){
      printf("debug: counted %d loop cycles the last 1000ms\n", cycleCount);
      cycleCount = 0;
      timestamp_lastCycleCountLogged = time_get_ms();
    } else {
      cycleCount++;
    }
#endif


  } // end while(1)

} // end main()

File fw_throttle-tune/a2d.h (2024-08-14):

#include <util/delay.h>
//#include "bsp_io.h"
//Vcc = 1023
//GND = 0
//
//Atmega8:
//PC5 = ADC5 = Channel 5
//PC4 = ADC4 = Channel 4
//PC3 = ADC2 = Channel 3
//PC2 = ADC2 = Channel 2
//PC1 = ADC1 = Channel 1
//PC0 = ADC0 = Channel 0

//example: value = ReadChannel(5);
uint16_t ReadChannel(uint8_t mux);

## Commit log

2024-08-13 Add kicad project for throttle-tune board
    [throttle-tune.kicad_pcb, throttle-tune.kicad_sch]
2024-08-13 Copy Atmega8 firmware project for throttle-tune board
2024-08-14 Add UART (functional), led blinking
2024-08-14 Add 10Bit Fast-PWM, Add adc
2024-08-14 pcb: schematic using supply motorcontroller (dropped)
    [throttle-tune.kicad_sch]
2024-08-14 pcb: finish schematic (9V, cut-suppy, filters)
    [throttle-tune.kicad_pcb, throttle-tune.kicad_sch]
2024-08-14 pcb: arrange components
    [throttle-tune.kicad_pcb, throttle-tune.kicad_sch]
2024-08-15 Add throttle scaling (works)
2024-08-15 pcb: finish layout, pcb2gcode, adj pins - milled pcb
    milled pcb and populated, works well but
    error with P-channel mosfet (missing NPN driver)
    [throttle-tune.kicad_pcb, throttle-tune.kicad_sch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]
2024-08-15 Rework main.c: Structure, logging, scaling
    [main.c]
2024-08-16 pcb: fix supply cutoff (add NPN), update layout
    Note: fixed in already milled pcb by adding transistor with wires
    [throttle-tune.kicad_pcb, throttle-tune.kicad_sch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]
2024-08-16 Add speed-switch support, fading, faster-resume duty
2024-08-20 pcb: optimize text, comments, Add README
    [throttle-tune.kicad_pcb, throttle-tune.kicad_sch]
2024-08-20 Add Photo of pcb
2024-09-29 Add schematic, 3d-model exports, Assign 3d-models
    [throttle-tune.kicad_pcb]
2025-01-26 Add text annotations for connecting, Update exports
    [throttle-tune.kicad_pcb, throttle-tune.step]
2025-03-22 Add buzzer output, beeps at startup
    [main.c]
2025-03-23 Replace register access with GPIO lib for speed switch
    [main.c]
2025-03-29 Add beeping at speed-sw-change, Outsource functions (beep, speet-sw), Update buzzer pin
    [main.c]
2025-04-21 Update Readme: Add tasks for next PCB version
2025-04-22 Add custom time lib (from e-kart proj), Rework fading using timestamps
    [main.c]
2025-04-22 Add custom pwm lib (from e-kart proj), Use outsourced pwm functions
2025-04-23 Add IDLE-voltage + separate reverse duty, Improve beeping, Adjust speed-level config while testing
    [main.c]
2025-04-26 Add spreadsheet for calculating fading options
    [calculate-fading.ods]
2025-05-01 Fix debug-output, Add cycle-time results, Adjust pedal, mem, avg options
    [main.c]
2025-05-01 Add custom controller-full-speed-duty threshold, Limit UART debug output to 500ms
2025-08-18 Remove unnecessary subfolder
    [calculate-fading.ods, throttle-tune.kicad_pcb, throttle-tune.kicad_sch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]
